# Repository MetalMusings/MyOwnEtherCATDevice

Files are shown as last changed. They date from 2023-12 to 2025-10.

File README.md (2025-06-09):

# MetalMusings EtherCAT device

This repository contains the EtherCAT devices I have designed, built and put in use in linuxcnc.

Everything should be here: 
- Schematics, PCB layouts, and what is needed to build the boards.
- Software tools to create an ESI-file and program the ESC eeprom. 
- Software tools to create the application running on a STM32F407VG.
- A big learning curve is hidden in here as well

I have (so far) used two different ESC ICs: LAN9252 and Ax58100. 
Both work, I can't really see a difference. 
The Ax58100 has a leg spacing of 0.4 mm, 0.5 mm for the LAN9252, if that matters.
On paper the Ax58100 has more builtin functionality like stepper motor drivers,
but the documentation is lacking. Or my understanding of the documentation is lacking.
The Ax58100 supposedly has more efficient access to registers and data.
The indirection scheme is the main objection to using LAN9252, I have read.
The LAN9252 is the true and tested IC of the two. If you don't know, go for the LAN9252.

The EtherCAT cards, which I call EaserCAT cards, use an EtherCAT chip and a normal MCU.
I have used the STM32F407VGT6. The EaserCAT chip does the network talk and other 
EtherCAT things. The STM32 does the application things, like reading and setting pins high or low,
reading encoder inputs, generate stepper motor pulses and other interesting applications one can think of.
There is a narrow interface between the two: SPI and a couple of lines for synchronization.
Any decent MCU can do that, it doesn't have to be a STM32F407VGT6. I have tested with a esp32 with success.
Feel free to experiment with other processors.

I learned most of what I know about EtherCAT through a number of Youtube videos I made.
There are accompanying git branches. For example, for video 8 you can check out the
Video8 branch to get the software tree in the state at the video.
More info on the videos, which are now more of historical interest, but also a bit of learning by following [this link](Videos.md)

And of course, this work builds on the work of many others. This would not be possible without their work. 
I'm just reusing what they did and maybe expanding on it.

Here is the start of [building instructions](Build.md)

## EaserCAT 2000 - a testbench for ESC+MCU, SOES, stepper generator, linuxcnc

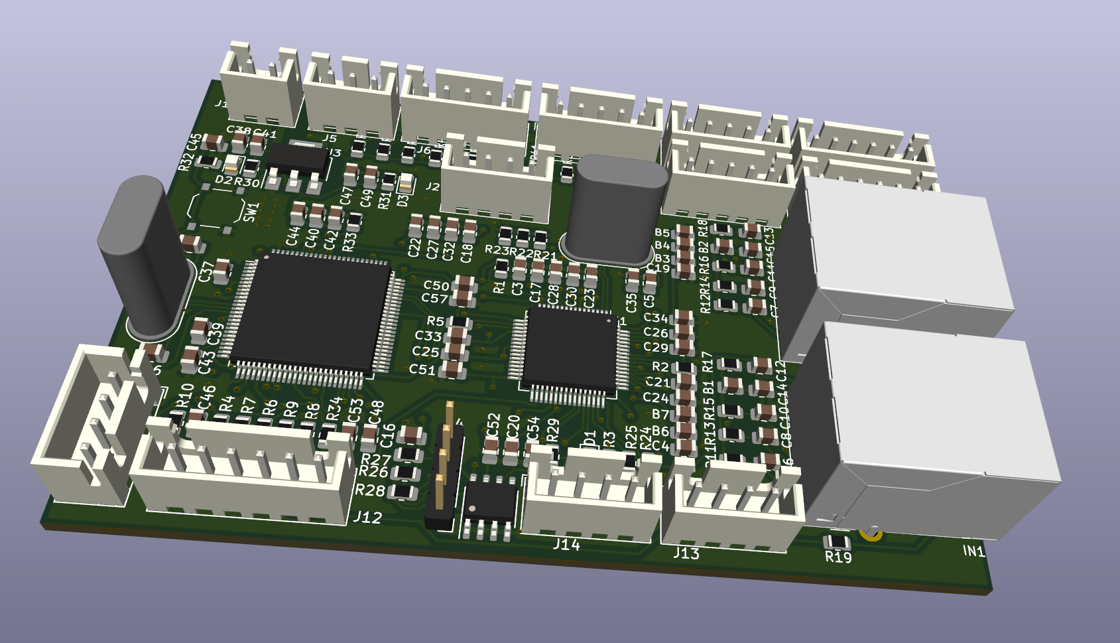
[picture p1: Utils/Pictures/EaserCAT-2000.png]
Picture of EaserCAT 2000 board


This was the first card that got used in Linuxcnc. Follow [link here](Cards/EaserCAT-2000/)
I think I got it working pretty well in the end. There was, and still is, an issue with
synchronization between the linuxcnc servo-loop and the ESC DC loop.
I don't remember the status of it anymore, it was some time ago I worked with it.
The main thing was that it lacked optocouplers and isolation for the external signals.

## EaserCAT 3000 - All in one board with Ax58100

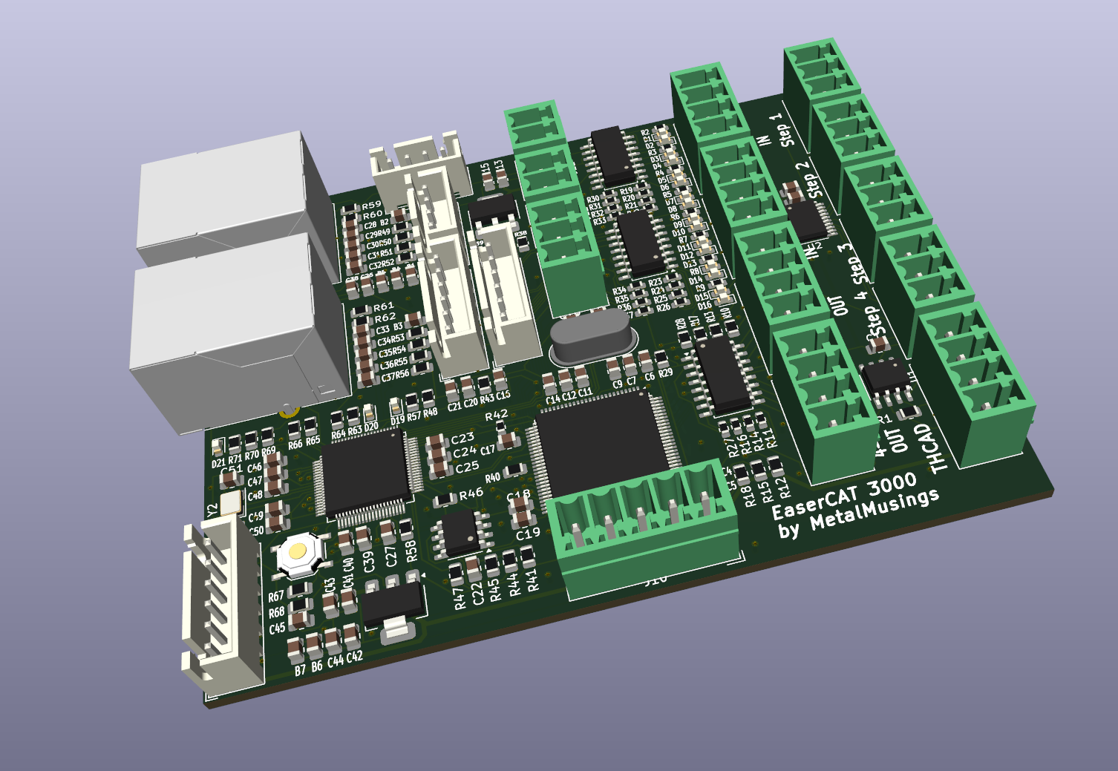
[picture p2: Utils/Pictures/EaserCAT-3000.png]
Picture of EaserCAT 3000 board


This card is an evolution of the EaserCAT 2000 and was intended to be used in my plasma cutter.
It features four stepper driver outputs, input for a THCAD arc voltage card, an encoder, 
an analog output (for spindle +- 10V), eight digital inputs, four digital outputs, 
plus some 12 I/O for any possible extension. The IOs are isolated from the MCU.

However, I couldn't get this card to work, almost at all. The Ax58100 didn't even load the eeprom. 
Struggling with the documentation for the Ax58100, which formed my negative opinion about that,
I gave up and let it sit for over half a year. It was first when someone came and asked 
questions around it I had another look. I built a new board, and it all started to work.
At time of writing it all seems to work.

The latest vesion of the firmware has all parameters for step generators as PDOs.

[Link here](Cards/EaserCAT-3000-Digital-Stepper-Analog-Encoder-Frequency/)

## EaserCAT 4000 - THCAD reader

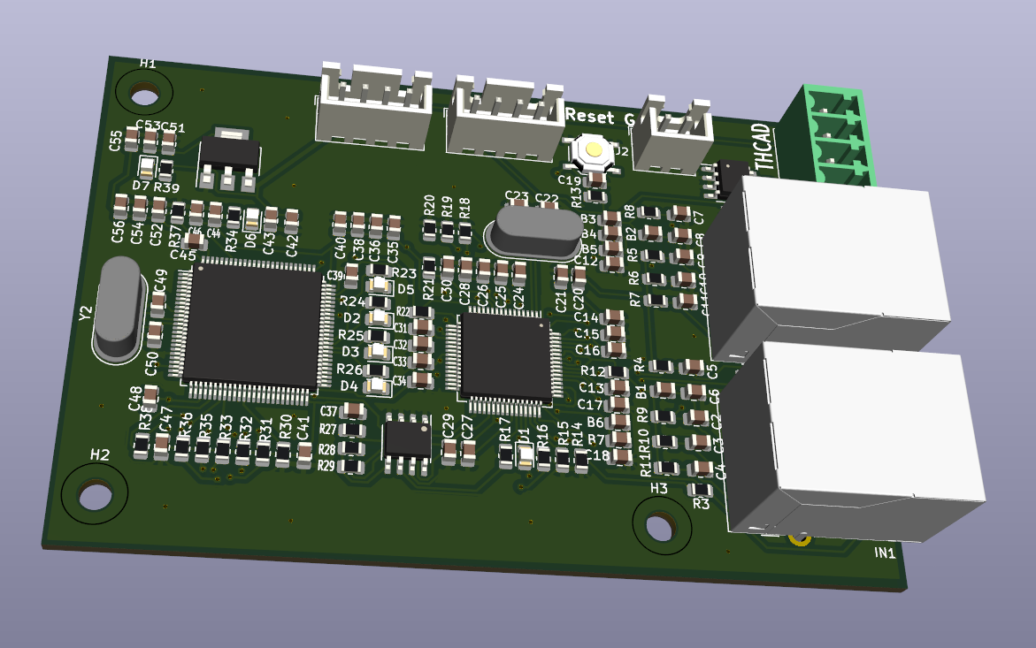
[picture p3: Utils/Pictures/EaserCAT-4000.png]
Picture of EaserCAT 4000 board


Faced with the problems with the EaserCAT 3000 board, and still wanting to use EtherCAT 
in my upcoming plasma cutter, I made this board whos single purpose is to read 
the PWM frequency from Mesa's THCAD board.\
The THCAD board reads the voltage between 
the plasma torch and the workpiece which is around 100V. Highly isolated, and with 
a voltage to frequency converter it delivers a differential pwm signal. 
The frequency of this signal can be related to the voltage.\
That's what is needed for linuxcnc torch height control.

In the tests on the bench this can read at least up to 200 kHz, but its's better to be below 100 kHz.
The THCAD has a frequency divider one can set to make the frequency range nicely match this.
It seems to work fine so far. 
Implementation is with interrupts. \
A better option would have been to use TIM2's PWM_INPUT function, which can work with several MHz frequency. 
I tried the PWM_INPUT method a lot but couldn't get it to work. The current method still works, though.
If time and interests are in phase with the moon, I might look at PWM_INPUT again.

This board is now relegated to history, replaced by the EaserCAT-6000.

[Link here](Cards/EaserCAT-4000-THCAD-Reader/)

## EaserCAT 5000 - Digital IO without MCU

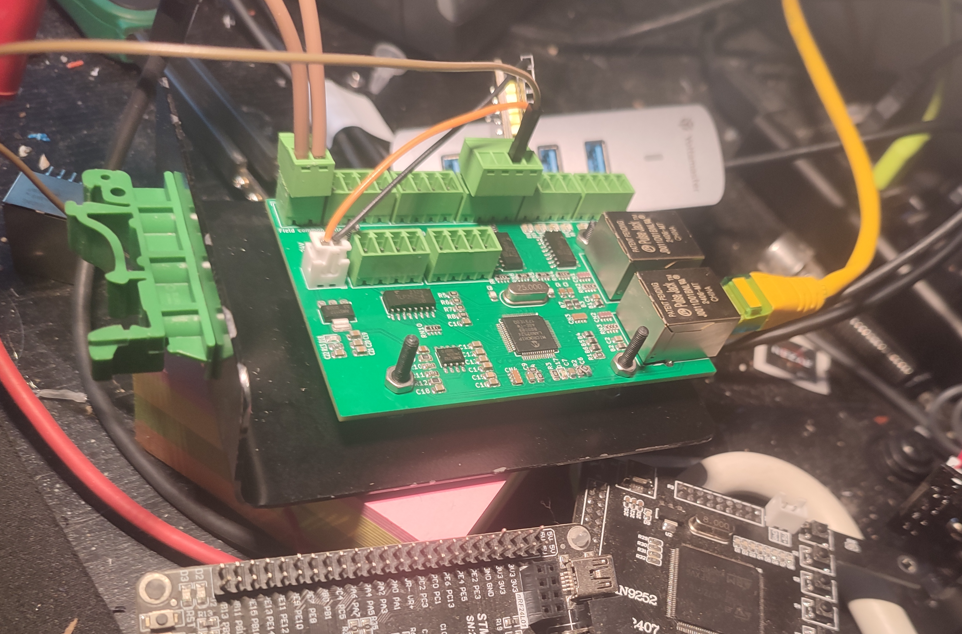
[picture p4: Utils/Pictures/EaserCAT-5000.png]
Picture of EaserCAT 5000 board


A card just doing Digital Input and Digital Output. The intentions were to read 
limit switches and some other switches around the plasma torch. And to switch on the plasma torch.
It's a single LAN9252, configured for local IO. Optocouplers are attached to IO pins for isolation.
It has been tested on the bench, it works with TwinCAT.

HOWEVER, it doesn't work, and will not work, with linuxcnc. As I've learned,
the IgH EtherCAT master needs a CoE client (CANopen over EtherCAT).
The LAN9252 in DIO mode is only an EtherCAT client and can't be turned
into a CoE client. And the IgH EtherCAT application interface for real-time
communication can not be downgraded to work with a pure EtherCAT client,
it requires a CoE client.

To add CoE functionality means to add number of objects at certain positions
in the client and that can not be done to the LAN9252. It is what it is.
In a setup with LAN9252 with MCU, those objects are created in the firmware,
so there it works.

This board is now relegated to history, replaced by the EaserCAT-6000.

## EaserCAT 6000 - Digital IO and frequency input

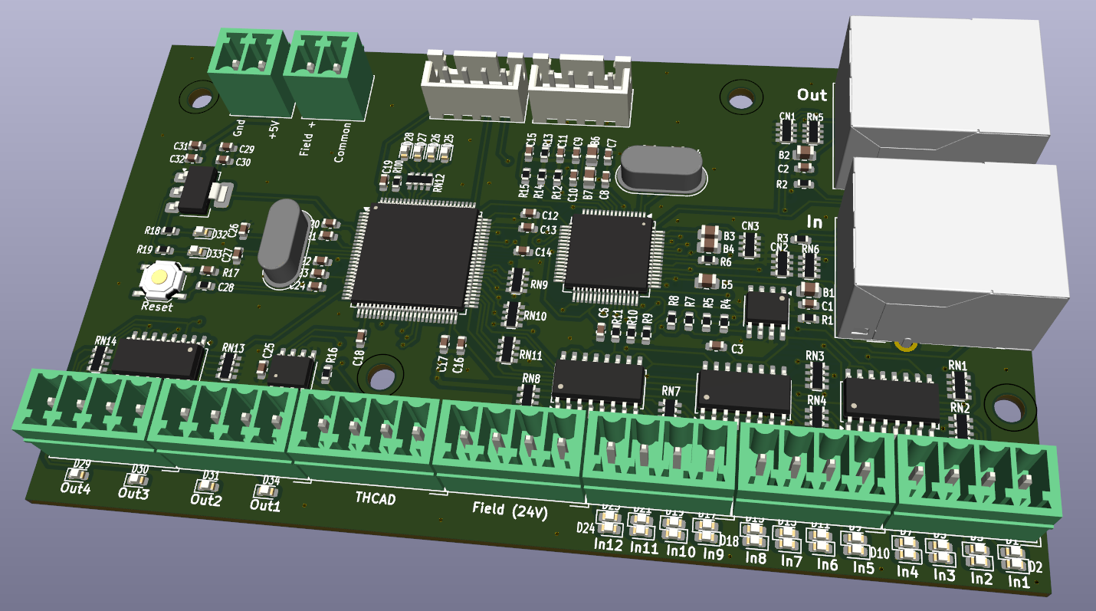
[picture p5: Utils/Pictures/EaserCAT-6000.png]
Picture of EaserCAT 6000 board


Finally, a card that's actually used in a real system. This card is used in my plasma cutter. 
It has 12 digital inputs, 4 digital outputs and a frequency counter to get
the input from Mesa's THCAD (reader of voltage between plasma nozzle and workpiece).\
All digital IOs are opto-isolated and the frequency input uses a RS-485 receiver.

In the plasma cutter, it does the job. There are three ECT60 stepper motor drivers.
And the EaserCAT-6000 card. It handles limit switches for X, Y and Z, floating switch,
break-away switch, and plasma Arc OK signal. There is room for e-stop and other switches.\
The plasma torch is switched on using one of the digital outputs.\
THCAD is an older model with full voltage input. Frequency divider is set to 1/32.

This board replaces EaserCAT-4000 and EaserCAT-5000. 

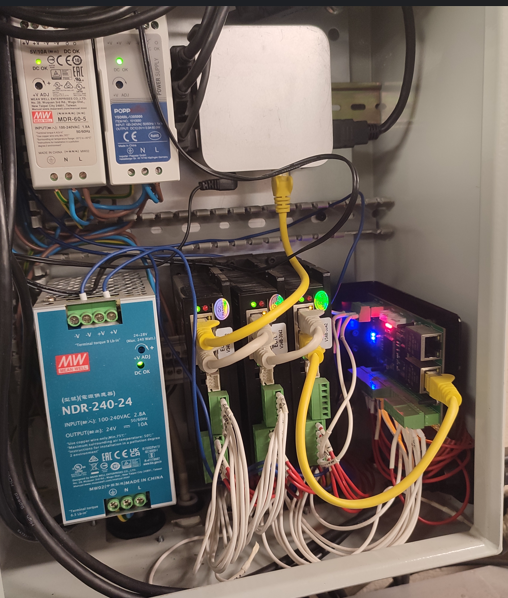
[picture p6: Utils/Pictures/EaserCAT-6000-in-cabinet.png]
Inside the cabinet


[Link here](Cards/EaserCAT-6000-THCAD-reader+Digital-IO/)

A few weeks later and I've used this card in the plasma cutter for quite a bit of cutting and it hasn't missed a beat. Works so well. THC follows the sheet surface up and down. Awesome.

## EaserCAT Torch Height Control - EaserCAT 7000 with THTIC and THTIC2

Actually something useful again - not one, but two, plasma torch voltage readers.
They replace the THCAD board and comes with the entire chain from voltage reading to the introduction of a calibrated voltage to linuxcnc for use in QtPlasmaC. 

Let's start with the plasma cutter. There is either a THTIC or THTIC2 mini-board, which reads the plasma torch voltage, and through a voltage divider lowers it to about 2 Volts during cutting. This voltage is converted by an analog to digital converter and feeds the digitized voltage to the EaserCAT 7000 board via an I2C bus (cable). The EaserCAT 7000 board makes the voltage available both as the raw read voltage for further scaling, or as a calibrated voltage using entered calibration constants.

The plasma torch voltage is DCEN - DC Electrode Negative. The workpiece ground is often connected to ground/earth.
With ground as the reference voltage, the plasma torch voltage ranges between 0 V and -200 V.
An inverting operational amplifier switches the polarity for the ADC. The ground planes on the circuit board are connected to the workpiece ground.

An important feature of THCTIC and THCTIC2 is that the plasma voltage side is isolated from the linuxcnc signal side. The isolation level is better than 1.5 kV. This is achieved by an I2C isolator and an isolated DC-DC converter. The difference between the two cards is the choice of ADC. THTIC uses MCP3221 and THTIC2 uses ADS1014. Both are 12-bit analog to digital converters, ADS1014 is perhaps an 11-bit, both with sampling rates around 3 kHz. A newly measured voltage value can be obtained every 1 ms. Of course you only choose one of the two. Since it seemed pretty easy when I did it, I made two different ones. Always good to have options.

The boards are relatively small, 42x30 mm. Voltage 5V in, current less than 10 mA. I2C Data and clock. 

### THTIC
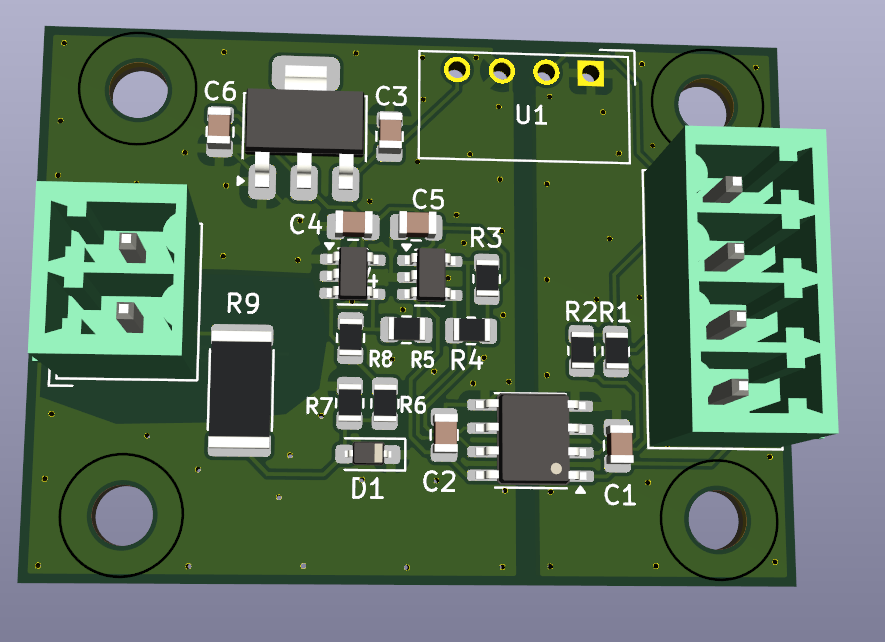
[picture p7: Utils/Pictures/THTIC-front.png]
THTIC
 
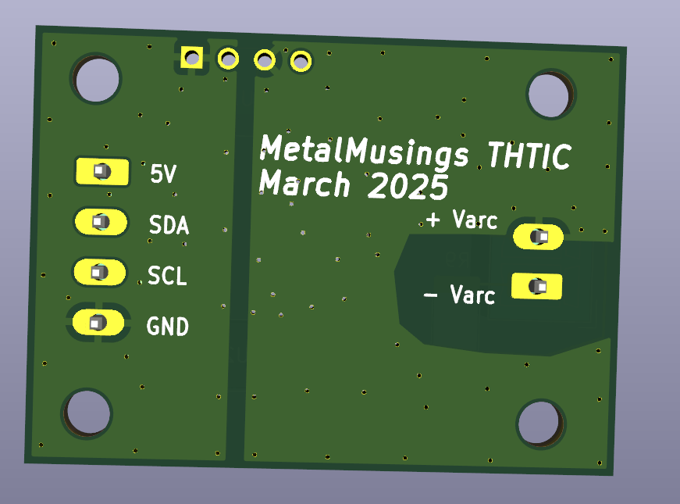
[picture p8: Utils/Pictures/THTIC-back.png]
THTIC


### THTIC2
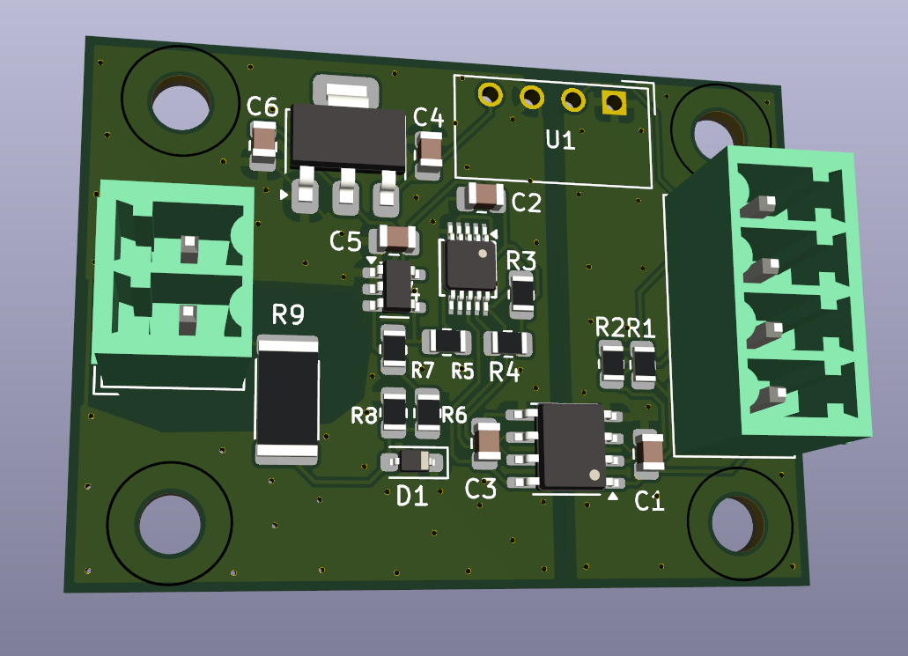
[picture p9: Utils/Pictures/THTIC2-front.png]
THTIC2
 
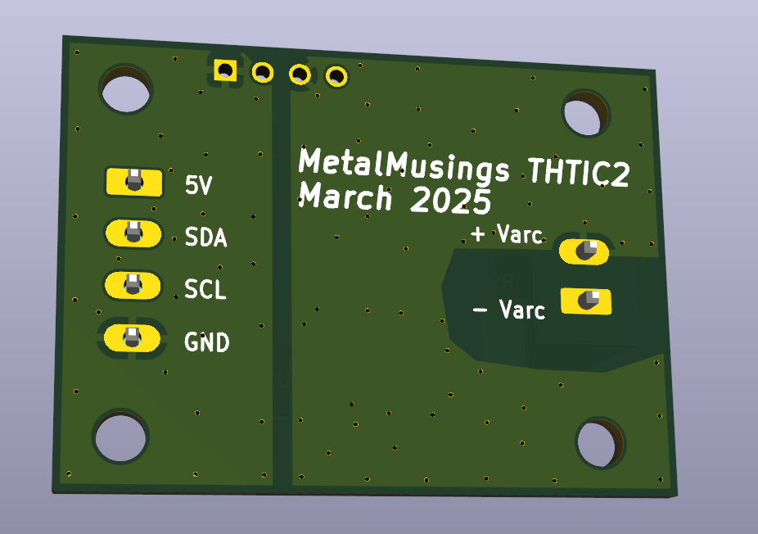
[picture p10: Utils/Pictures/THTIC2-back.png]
THTIC2


### EaserCAT-7000 Digital IO and I2C voltage reader
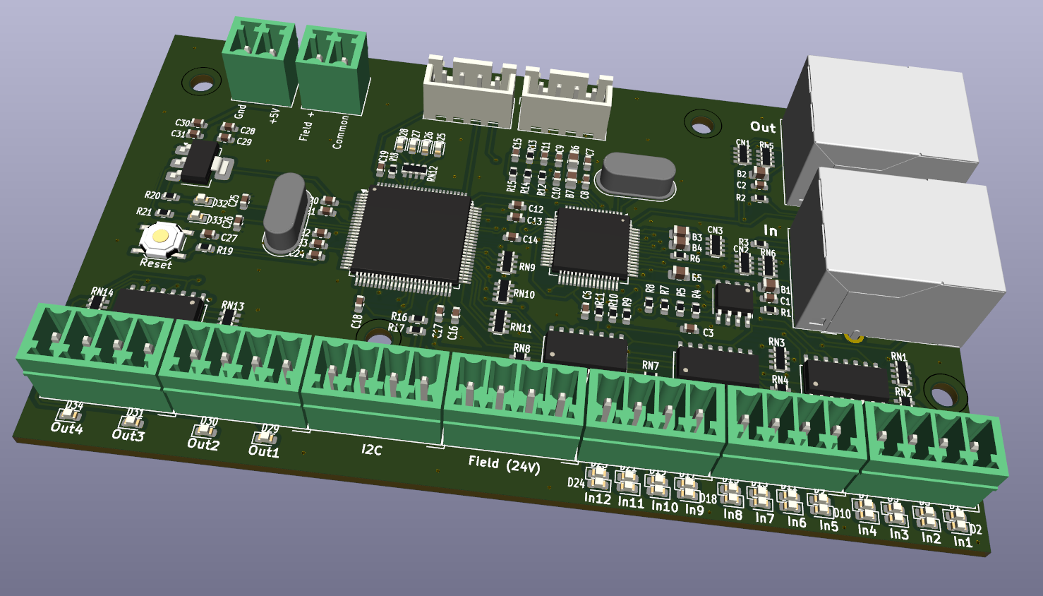
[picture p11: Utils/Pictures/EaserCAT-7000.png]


EaserCAT-7000 is an EaserCAT-6000 board where the THCAD frequency input has been replaced by the I2C bus.
There are twelve digital inputs and four digital outputs.

Currently the EaserCAT-7000 can handle two I2C voltage readers, on different I2C addresses.\
Configuration of the connected I2C devices is done by setting the voltage reader type in SDOs 0x2000:1 and 0x2001:1 for device 1 and 2. The I2C device type is set to 0 by default. A zero means no I2C ADC. Entering a 1 in 0x2000:0 selects the MCP3221, and a 2 in 0x2000:0 selects the ADS1014.\
The I2C address for the ADC is written into SDOs 0x2000:2 and 0x2001:2. The address for the MCP3221 is selected when it is purchased - there are 8 different models each with a different I2C address 0x48-0x4f. The THTIC2 board has the address fixed at 0x48; can be modified during pcb assembly to 0x49 quite easily - check datasheet. Short version is to cut Addr-Gnd and add Addr-Vcc.

Pay attention to the polarity when connecting the plasma voltage leads the THTIC and THTIC2. Varc+ must have higher voltage potential the Varc- (as one would expect). The voltage divisor may need to be adjusted, there is now one 100 kOhm resistor and a 2.2 kOhm resistor, which brings down 100 V to around 2 V. Adjust as needed. For high voltage, pay attention to the max allowed voltage of the resistor. The ADC likes to have around 2-3 Volts when cutting.

The experience with these cards has been very good. I used the THTIC a lot, cutting for at least an hour of cutting time, with THC enabled and active. A status variable shows that it has been working the whole time, no stops or resets. After that I switched to the THTIC2 card and have been using that since. Works really well.

## THCLIP Enable ohmic sensing with the IPTM-60 torch

This is for the torches known as IPT-60 PT-60 S45 IPTM-60 IPTM-80 and many more that have blowback start with the torch tip exposed and normally shortened to the torch electrode. Normally this torch can't use ohmic sensing since all parts are connected to ground. At least on my machine, a Herocut 8000, the blowback start cable from the torch can be cut during sensing. This enables ohmic sensing and it continues to operate in other situations.

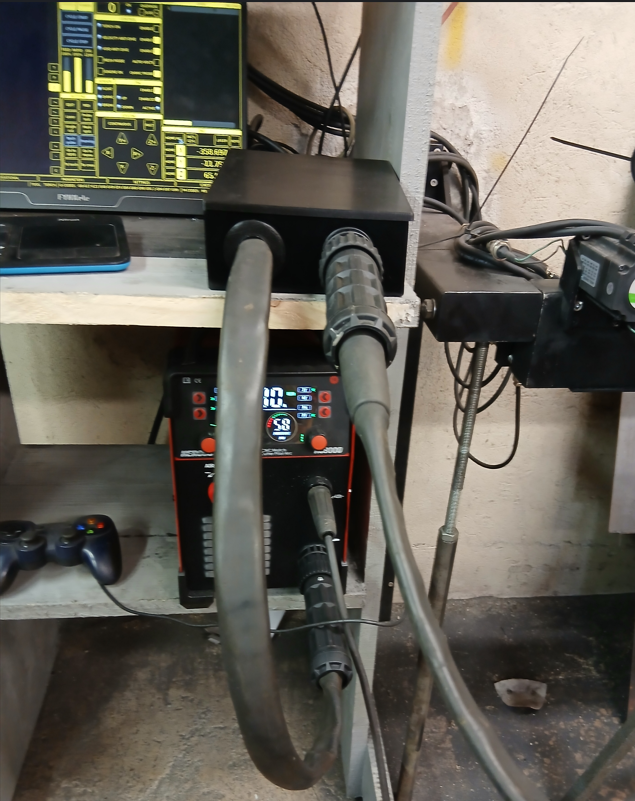
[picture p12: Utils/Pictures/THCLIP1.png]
THCLIP


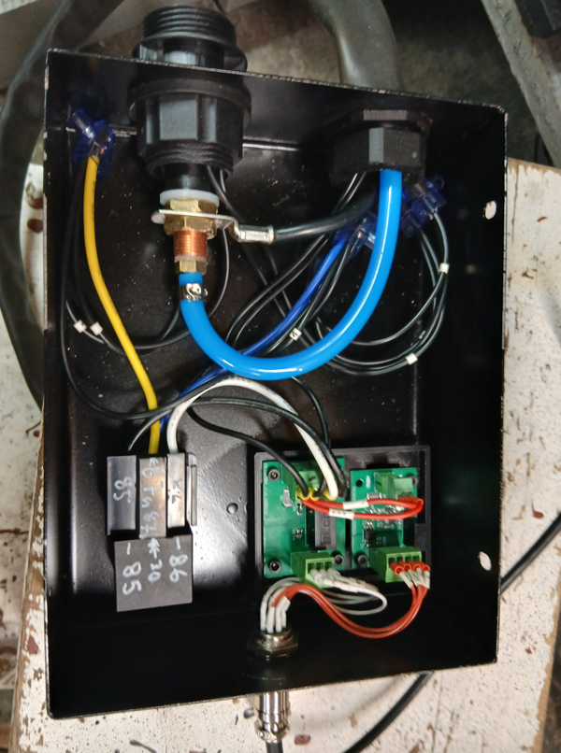
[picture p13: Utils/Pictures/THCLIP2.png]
THCLIP


I tried at first to use the normal Arc voltage reader to detect any contact between the torch and the work piece during probing. However, that was not reliable - it seems there is electronics involved with the arc voltage. Don't want to know details. 

I put a second voltage reader THTIC2 close to the THCLIP and measure the 24V applied after the relay. Monitoring this voltage turns out to be reliable and makes the ohmic sensing work really well.

I have made an adaptation to the EaserCAT 7000 to handle the contact. The relay has a short, some 10 msecs, setup time. The read voltage must therefor first go above the voltage limit before it starts to scan for the voltage to go below the voltage limit which indicates contact.

The Trafimet torch hose connectors are called FY0022 and FY0023. The relay is a 24V 40A standard car relay. Check out the Kicad schematics for the other parts.

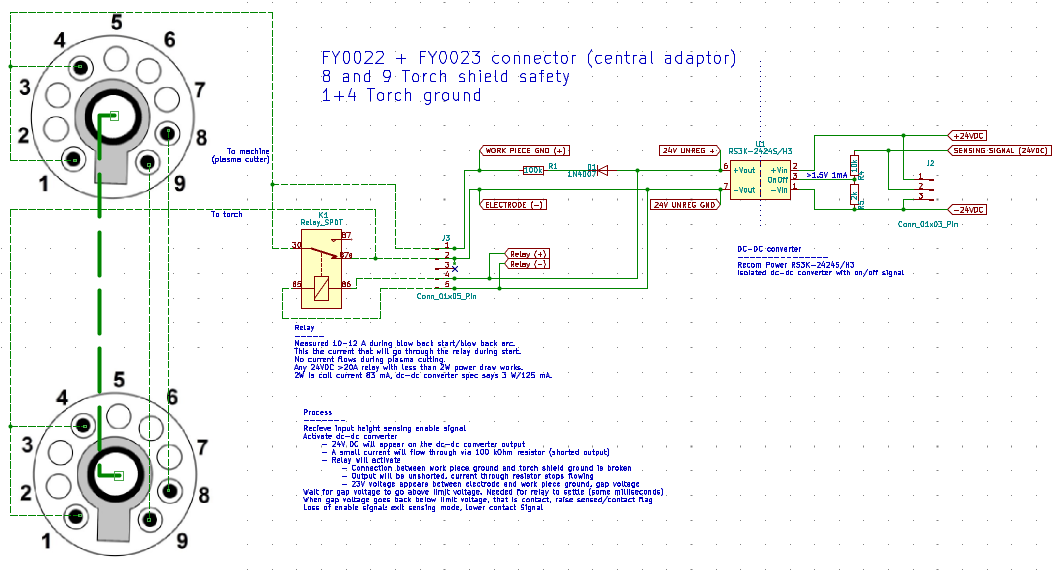
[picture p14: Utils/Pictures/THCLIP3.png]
Schema

Leads 1 and 4 are the blowback arc start ground leads in my torch. They get cut by the relay during ohmic sensing. Voltage is measured on connector J3, between pin 1 and pin 2.

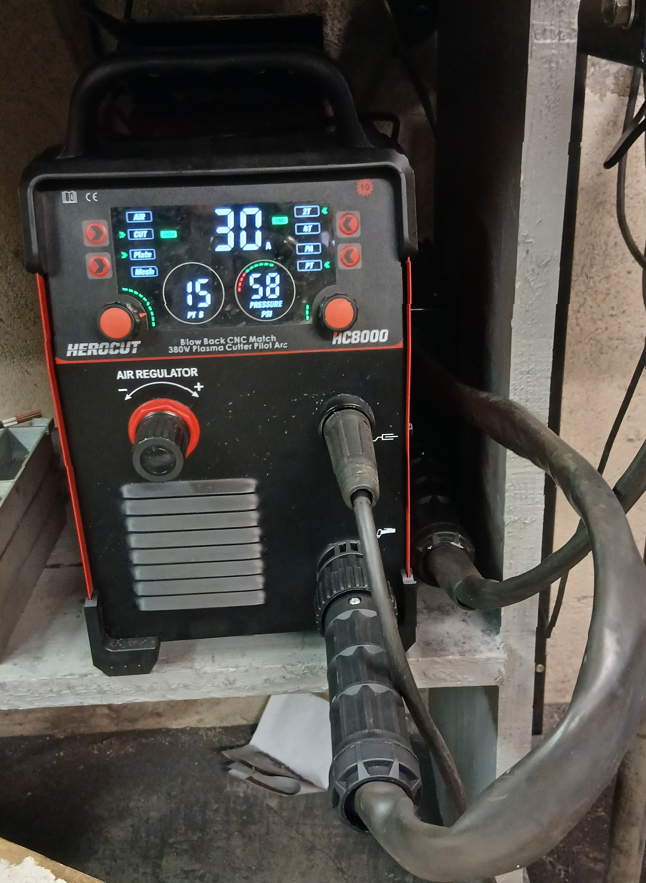
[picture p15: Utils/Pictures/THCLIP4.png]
Ready for use


## License

Don't violate the original licenses. No warranties. Use it any way you like.\
Remember: It is a hobby project, not a product.

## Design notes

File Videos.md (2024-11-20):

# Making my own EtherCAT device

This repository contains software, pcb shematics and layouts, reference documentation etc
that I used during the creation of my own EtherCAT device.

This job is documented in a series of Youtube videos, from my first attempts to understand
how EtherCAT works, to making my own pcb, program it and testing it in LinuxCNC.

=======
The links are now pointing to nowhere. Checkout a Video branch,  Video8, and it might work
=======

## Make my own EtherCAT device 9. About time. Step generator

This was something, I almost gave up. But here it is. A working step generator.
Actually, not one but two step generators for the EaserCAT 2000 board.
For a step generator it is all about timing, timing and timing.
I'll walk you through what I had to do to get it to work.
It can give some general insight into how EtherCAT for linuxcnc works.

Biggest changes this time are in the [Firmware folder](Firmware).
The [Documentation folder](Documentation) has design details on the second step generator.
A small but fatal indexing bug was fixed in the EEPROM_generator.
For all details, read the git log. Too much to mention all.

Watch the video (https://youtu.be/lBDBcseFki8)

## Make my own EtherCAT device 8. EaserCAT 3000

Introducing the new **EaserCAT 3000** board. It's an evolution of the EaserCAT 2000
and intended to be used in my plasma cutter. It features four stepper driver outputs,
input for a THCAD arc voltage card, an encoder, an analog output (for spindle +- 10V),
eigth digital inputs, four digital outputs, plus some 12 I/O for any possible extension.

The KiCAD files are in the [KiCAD folder](Kicad/Ax58100-stm32-ethercat)

Watch the video (https://youtu.be/boanv6ihYtI)

## Make my own EtherCAT device 7. Turning in the lathe

I have now put things together so the EaserCAT 2000 card controls
my small CNC lathe. Two stepper generators, one each for the X and Z axes,
and an encoder counter for the spindle encoder are on this small card.

While it works there are still issues caused by the variation in cycle time. Thankfully
I was able to reduce the variation from 80-100 microseconds down to 2-3 microseconds,

Watch the video (https://youtu.be/Bqi1KXEVI1Q)

## Make my own EtherCAT device 6. Stepper motor driver

The stepper driver generator shows up and makes some stepper motor sounds. The two big things
this time have been setup of the timer for the stepper pulses and synchronizing the EtherCAT
cycle with the linuxcnc servo-thread cycle. Thankfully I don't show much of that.

Watch the video (https://youtu.be/QNNEA0wO4Mw)

## Make my own EtherCAT device 5. The lathe is alive

I hook up the EaserCAT 2000 board to my mini-lathe and make it work.
Documentation is available here, please select the *Video5* branch.

Watch the video (https://youtu.be/wOtMrlHCCic)

## Make my own EtherCAT device 4. The PCB is here

In this video it starts to be interesting. I have got the pcb and I try to make it work.
Now I finally make documentation available, see [this folder](Pcb-1-lan9252).

Watch the video (https://youtu.be/An0VrKYAv88)

## Make my own EtherCAT device 3. Encoder

I made a rudimentary EtherCAT encoder module. To test it I need something better than my test setup so I start to design my own PCB to be used for testing with LinuxCNC.

Watch the video (https://youtu.be/oNIBOpeTpQ4)

## Make my own EtherCAT device. 2. MCU and SPI

Testing the SPI connection between the MCU and the LAN9252 chip. Get into state diagrams for EtherCAT and for CIA402.

Watch the video (https://youtu.be/F9HdCEG6kow)

## Make my own EtherCAT device. 1 Digital IO

My first tries with the LAN9252 chip. Getting accustomed to some tools.

Watch the video (https://youtu.be/IGmXsXSSA4s)

# EtherCAT PCB based on LAN9252 and STM34F407

##### The firmware is in the **Firmware** folder.

Open this in PlatformIO. PlatformIO might be able to install all necessary software. If not, you need at least Arduino for STM32 (STM32duino) and SPI. PlatformIO might be able to figure that out, I hope so.
SPI settings are in lib/soes/hal/spi.cpp if you are interested.
SOES is the Arduino port of SOES from <https://github.com/kubabuda/ecat_servo/tree/main/examples/SOES_arduino>
My own code is in main.cpp. The encoder counter code is in STM34_Encoder.cpp

###### The PCB design is in **Kicad**.

Open this with Kicad. I have put the symbols and footprints in there, just set the right paths.
The design is in the state I ordered the pcb from Aisler, Germany.

###### The **Schematics** folder

contains reference documentation, schematics of several LAN9252 evaluation boards and other boards. This is from where I got inspiration and ideas to the design. No I didn't read all the reference documentation - I copied most from these designs and that's why it also worked the first time. [Freerouting](https://github.com/freerouting/freerouting) was used to route the pcb. Normally I route the nets by hand but this time it was a bit much and it came out quite nice and, most importantly, it worked. 

##### ESI xml file generator is in **EEPROM_generator**.

Access the folder with a file browser and click on index.html to make or update your own xml file (and other necessary files, incl eeprom bin). Copy the contents to Firmware/lib/soes
and to Twincat esi xml file directory `c:\twincat\3.1\io\modules\ethercat`
The original EEPROM_generator is found here <https://github.com/kubabuda/EEPROM_generator>

##### **CubeMX-files** are for reference only.

The .ioc file can be opened in CubeMX. The STM32F407 processor has functions tied to specific pins, the .ioc file has this info. This is just for reference.

##### ESI (EtherCAT Slave Information) files

I have put [Dig_8IN_8OUT.xml](Dig_8IN_8OUT.xml) here, this is an example ESI file for the LAN9252 IC standalone, no MCU needed. It's sometimes handy to have the simplest possible ESI file at ahnd, here it is. You find the ESI file for the Encoder application [here](Firmware/lib/soes/MetalMusings_EaserCAT_2000_encoder.xml)

##### **linuxcnc** contains modifications to make EaserCAT 2000 work

The configuration files and the hal component I used are placed here.

##### LAN9252_eeprom_store_valid

Arduino sketch to program the AT24C32 eeprom with a valid eeprom content. Hook up the eeprom using I2C and run the program. The verification in the of theprogram must be passed for valid programming.

###License

Don't violate the original licenses. No warranties. Use it any way you like.

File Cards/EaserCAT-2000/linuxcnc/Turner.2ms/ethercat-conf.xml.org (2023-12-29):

<masters>
  <master idx="0" appTimePeriod="1000000" refClockSyncCycles="5">
    <slave idx="0" type="EK1100"/>
    <slave idx="1" type="EL1008"/>
    <slave idx="2" type="EL2008"/>
    <slave idx="3" type="EL5101"/>
    <slave idx="4" type="generic" vid="00000a88" pid="0a880002" configPdos="true">
      <dcConf assignActivate="300" sync0Cycle="*1" sync0Shift="0"/>
      <sdoConfig idx="2000" subIdx="0"><sdoDataRaw data ="b8 0b"/></sdoConfig>  <!-- Max motor current (3.0A) -->
      <sdoConfig idx="2003" subIdx="0"><sdoDataRaw data ="64 00"/></sdoConfig>  <!-- Standby current percentage (100%) -->
      <sdoConfig idx="2011" subIdx="0"><sdoDataRaw data ="00 00"/></sdoConfig>  <!-- Open loop -->
      <syncManager idx="2" dir="out">
        <pdo idx="1600">
          <pdoEntry idx="6040" subIdx="00" bitLen="16" halPin="cia-controlword" halType="u32"/>
          <pdoEntry idx="6060" subIdx="00" bitLen="8" halPin="opmode" halType="s32"/>
          <pdoEntry idx="607A" subIdx="00" bitLen="32" halPin="target-position" halType="s32"/>
          <pdoEntry idx="60FF" subIdx="00" bitLen="32" halPin="target-velocity" halType="s32"/>
        </pdo>
      </syncManager>
      <syncManager idx="3" dir="in">
        <pdo idx="1a00">
          <pdoEntry idx="6041" subIdx="00" bitLen="16" halPin="cia-statusword" halType="u32"/>
          <pdoEntry idx="6061" subIdx="00" bitLen="8" halPin="opmode-display" halType="s32"/>
          <pdoEntry idx="6064" subIdx="00" bitLen="32" halPin="actual-position" halType="s32"/>
          <pdoEntry idx="606C" subIdx="00" bitLen="32" halPin="actual-velocity" halType="s32"/>
          <pdoEntry idx="6077" subIdx="00" bitLen="32" halPin="actual-torque" halType="s32"/>
        </pdo>
	</syncManager>
    </slave>
    <slave idx="5" type="generic" vid="00000a88" pid="0a880002" configPdos="true">
      <dcConf assignActivate="300" sync0Cycle="*1" sync0Shift="0"/>
      <sdoConfig idx="2000" subIdx="0"><sdoDataRaw data ="68 10"/></sdoConfig>  <!-- Max motor current (4.2A) -->
      <sdoConfig idx="2003" subIdx="0"><sdoDataRaw data ="64 00"/></sdoConfig>  <!-- Standby current percentage (100%) -->
      <sdoConfig idx="2011" subIdx="0"><sdoDataRaw data ="00 00"/></sdoConfig>  <!-- Open loop -->
      <syncManager idx="2" dir="out">
        <pdo idx="1600">
          <pdoEntry idx="6040" subIdx="00" bitLen="16" halPin="cia-controlword" halType="u32"/>
          <pdoEntry idx="6060" subIdx="00" bitLen="8" halPin="opmode" halType="s32"/>
          <pdoEntry idx="607A" subIdx="00" bitLen="32" halPin="target-position" halType="s32"/>
          <pdoEntry idx="60FF" subIdx="00" bitLen="32" halPin="target-velocity" halType="s32"/>
        </pdo>
      </syncManager>
      <syncManager idx="3" dir="in">
        <pdo idx="1a00">
          <pdoEntry idx="6041" subIdx="00" bitLen="16" halPin="cia-statusword" halType="u32"/>
          <pdoEntry idx="6061" subIdx="00" bitLen="8" halPin="opmode-display" halType="s32"/>
          <pdoEntry idx="6064" subIdx="00" bitLen="32" halPin="actual-position" halType="s32"/>
          <pdoEntry idx="606C" subIdx="00" bitLen="32" halPin="actual-velocity" halType="s32"/>
          <pdoEntry idx="6077" subIdx="00" bitLen="32" halPin="actual-torque" halType="s32"/>
        </pdo>
	</syncManager>
    </slave>
    <slave idx="6" type="generic" vid="00aaa" pid="000bbbccc" configPdos="true">
      <dcConf assignActivate="300" sync0Cycle="*1" sync0Shift="0"/>
      <syncManager idx="2" dir="out">
        <pdo idx="1600">
          <pdoEntry idx="7000" subIdx="00" bitLen="32" halPin="enc-pos-scale" halType="s32"/>
        </pdo>
        <pdo idx="1601">
          <pdoEntry idx="7001" subIdx="00" bitLen="32" halPin="enc-index-latch-enable" halType="u32"/>
        </pdo>
      </syncManager>
      <syncManager idx="3" dir="in">
        <pdo idx="1a00">
          <pdoEntry idx="6000" subIdx="00" bitLen="32" halPin="enc-position" halType="float-ieee"/>
        </pdo>
        <pdo idx="1a01">
          <pdoEntry idx="6001" subIdx="00" bitLen="32" halPin="enc-frequency" halType="float-ieee"/>
        </pdo>
        <pdo idx="1a02">
          <pdoEntry idx="6002" subIdx="00" bitLen="32" halPin="DiffT" halType="u32"/>
        </pdo>
        <pdo idx="1a03">
          <pdoEntry idx="6003" subIdx="00" bitLen="32" halPin="index-byte" halType="u32"/>
        </pdo>
        <pdo idx="1a04">
          <pdoEntry idx="6004" subIdx="00" bitLen="32" halPin="index-status" halType="u32"/>
        </pdo>
      </syncManager>
    </slave>
  </master>
</masters>

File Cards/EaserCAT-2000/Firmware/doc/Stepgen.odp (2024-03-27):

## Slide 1

Position(Real)

stepPosition(Integer)

cycleTime

Time

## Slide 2

Position(Real)

stepPosition(Integer)

Initial condition

”scale” is known = steps/mm

initialPosition

initialStepPosition

cycleTime

Time

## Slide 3

Position(Real)

stepPosition(Integer)

End condition

”scale” is known = steps/mm

initialPosition

initialStepPosition

commandedPosition - 3 examples here

cycleTime

Time

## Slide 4

Position(Real)

stepPosition(Integer)

StepPosition for end

”scale” is known = steps/mm

commandedPosition - 3 examples here

stepPosition =

floor(commandedPosition*scale)

initialPosition

initialStepPosition

cycleTime

Time

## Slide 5

Position(Real)

stepPosition(Integer)

Check for no step

”scale” is known = steps/mm

if initialStepPosition == stepPosition

take no step

goto update and return success

commandedPosition

stepPosition

initialPosition

initialStepPosition

cycleTime

Time

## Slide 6

Position(Real)

stepPosition(Integer)

Check for too many steps

too high frequency

”scale” is known = steps/mm

commandedPosition

stepPosition

initialPosition

initialStepPosition

commandedPosition

stepPosition

approximateFrequency = abs(initialStepPosition - commandedStepPosition)/cycleTime

if approximateFrequency > maxAllowedFrequency

take no step

goto update and return error

cycleTime

Time

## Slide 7

Position(Real)

stepPosition(Integer)

Line equations

”scale” is known = steps/mm

intitialStepPosition != stepPosition

frequency slow enough

commandedPosition

commandedStepPosition

stepPos = k Time + m

k = (commandedPosition - initialPosition)/cycleTime

m = initialPosition

Time = 0 at initial Time (nominal lcnc time)

initialPosition

initialStepPosition

cycleTime

Time

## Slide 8

Position(Real)

stepPosition(Integer)

Check for too flat slope

”scale” is known = steps/mm

intitialStepPosition != stepPosition, must take step

frequency slow enough

commandedPosition

stepPosition

Avoid problems with numerical precision at flat slope.

k * cycleTime * scale = amount of a step to take

if that amount < 0.01 (for example), just take a step in the

right direction half-way into cycleTime.

We know we must take a step due to previous checks.

initialPosition

initialStepPosition

cycleTime

Time

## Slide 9

Position(Real)

stepPosition(Integer)

Tstart

”scale” is known = steps/mm

intitialStepPosition != stepPosition, must take step

frequency range ok

Tstart

For positive k:

Tstart = ((InitialStepPosition+1)/scale - m)/k

For negative k:

Tstart = (InitialStepPosition/scale - m)/k

initialPosition

initialStepPosition

Tstart

cycleTime

Time

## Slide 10

Position(Real)

stepPosition(Integer)

Frequency

”scale” is known = steps/mm

intitialStepPosition != stepPosition, must take step

frequency range ok

Tstart is known

Tstart

initialPosition

initialStepPosition

Frequency = slope of curve, k * scale

Frequency = k * scale

Tstart

cycleTime

Time

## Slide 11

Position(Real)

stepPosition(Integer)

Number of steps

and direction

”scale” is known = steps/mm

intitialStepPosition != stepPosition, must take step

Frequency range ok

Tstart is known

Frequency is known

commandedPosition

commandedStepPosition

nSteps = commandedStepPosition - initialStepPosition

sign(nSteps) = direction

sign(k) = direction

commandedPosition

stepPosition

Tstart

initialPosition

initialStepPosition

Tstart

cycleTime

Time

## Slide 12

Position(Real)

stepPosition(Integer)

Prepare for next cycle

initialPosition <= commandedPosition

initialStepPosition <= commandedStepPosition

initialPosition

initialStepPosition

initialPosition

initialStepPosition

initialPosition

initialStepPosition

cycleTime

Time

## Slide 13

Position(Real)

stepPosition(Integer)

Pulses

Tstart

T=1/frequency

Tstart

Tstart

Tstart

Tstart

cycleTime

Time

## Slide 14

Position(Real)

stepPosition(Integer)

Pulses

Note. Time scale is different in this and following slides

T=0 is measured from SM2 interrupt, which seems to happen within 2-3 μsecs

Therefor, Tjitter = 5 μsecs

Pulse train is defined by

Tstart + Tjitter

frequency

nSteps

cycleTime

Tjitter

Tstart

Tstart

T=1/frequency

Tstart

Tjitter

Tjitter

Tstart

Tstart

Tstart

Time

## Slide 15

Position(Real)

stepPosition(Integer)

Starting the pulse train

Note. Time scale is different in this and following slides

Use HardwareTimer (stm32duino)

Take one of the 1-channel timers 10,11,13,14 on STM32F4 (AN4013)

startTimer->attachInterrupt(startTimerCB); // At constructor time

startTimer->setOverflow(Tjitter+Tstart, MICROSEC_FORMAT); // Now

startTimer->ressume(); //

Let the timer run for Tjitter+Tstart usecs, then it calls startTimerCB (below)

pulseTimer->setMode(pulseTimerChan, TIMER_OUTPUT_COMPARE_PWM2, stepPin);

pulseTimer->setOverflow(uint32_t(frequency), HERTZ_FORMAT);

pulseTimer->setCaptureCompare(pulseTimerChan, 50, PERCENT_COMPARE_FORMAT); // 50%

pulseTimerSteps = abs(nSteps);

pulseTimer->resume();

// Use local copy of nSteps, so it doesn’t accidentally gets overwritten.

cycleTime

Tjitter

Tstart

Tstart

T=1/frequency

Tstart

Tjitter

Tjitter

Tstart

Tstart

Tstart

Time

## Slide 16

Position(Real)

stepPosition(Integer)

Ending the pulse train

Note. Time scale is different in this and following slides

PulseTimer runs and calls pulseTimerCB at end of every PWM pulse

Number of steps to do are counted down and when 0, stop the pulseTimer

--timerPulseSteps;

if (timerPulseSteps == 0)

pulseTimer->pause();

cycleTime

Tjitter

Tstart

Tstart

T=1/frequency

Tstart

Tjitter

Tjitter

Tstart

Tstart

Tstart

Time

Problem with this approach

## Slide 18

Position(Real)

stepPosition(Integer)

The end is unpredictable and collides with next step’s pwm train

Tstart can be predicted accurately

The end of the pulse train also, Tend = Tstart + nStep / frequency

A problem occurs when Tstart,2 happens before Tend (Tstart,2 = Tstart for the next cycle)

At Tstart and Tstart,2 the pwm timer is reloaded. If that happens before the pwm pulse train is finished, problems occur.

At constant speed, every 1 ms we see a part of an overall long pulse train, just take a 1 ms piece and make pulses.

That’s what this procedure does. This works generally fine at constant speed, I think.

At increased and decreased speed, during acceleration, Tstart,2 is not what one think at first. It will be shorter or longer

and the situation described above occurs, when the pwm timer gets reloaded before it is finished.

The rising edge of the pwm pulse is in the right place, but everything that comes may not be.

It can not be like that.

Tend

cycleTime

Tjitter

Tstart,2

Tstart

Tstart

T=1/frequency

Tjitter

Tjitter

Tstart

Tstart

Tstart

Time

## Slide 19

Remedies

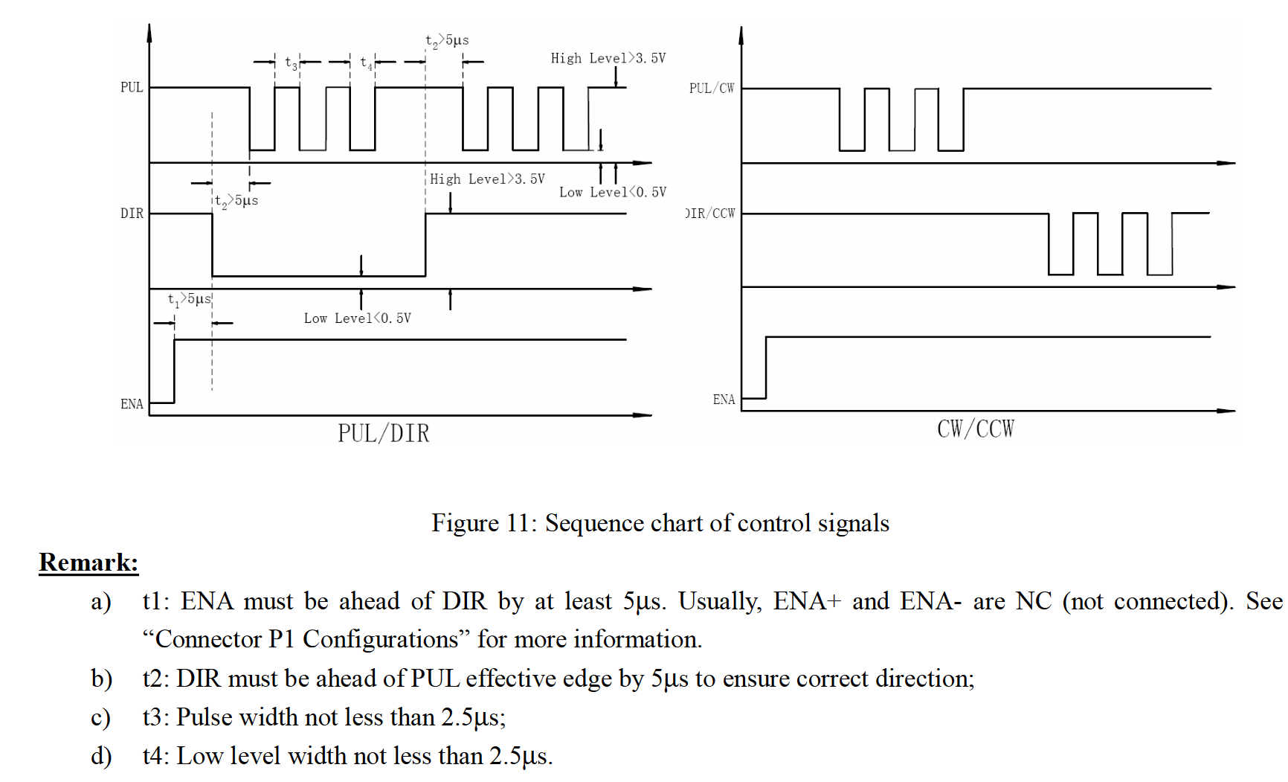
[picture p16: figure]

1. Skip Tstart and distribute pulses inside cycleTime window, keeping clear of the start and end

2. Modify pulse shape to use the most narrow pulse allowed by the driver

3. Don’t check for complete pulse at period update, but on capture/compare.

4. Keep frequency as before

5. Use end time of previous pulse when setting the time for the first pulse

Not perfect.

It will often happen that there are n and n+1 pulses in adjacent cycles. This will result in frequency jumping up and down.

2.5+2.5 usec => 5 usec and max 200 kHz. I don’t need that much. Say 5+5 usecs => max 100 kHz.

cycleTime

Tjitter

T=1/frequency

Interrupt here

## Timer

  >> f=[1 10 20 30 40 50 60 70 80 90 100]*1e3
  f = 1000 10000 20000 30000 40000 50000 60000 70000 80000 90000 100000
- >> fo=[956 9560 18390 27111 35768 44461 53221 61898 70539 79367 88000]
- fo = 956 9560 18390 27111 35768 44461 53221 61898 70539 79367 88000
- >> plot(f,fo, f, f, [f(end) 0],[fo(end) 1000])
- >> k=(fo(end)-1000)/f(end)
- k = 0.8700
- >> m=1000
- m = 1000

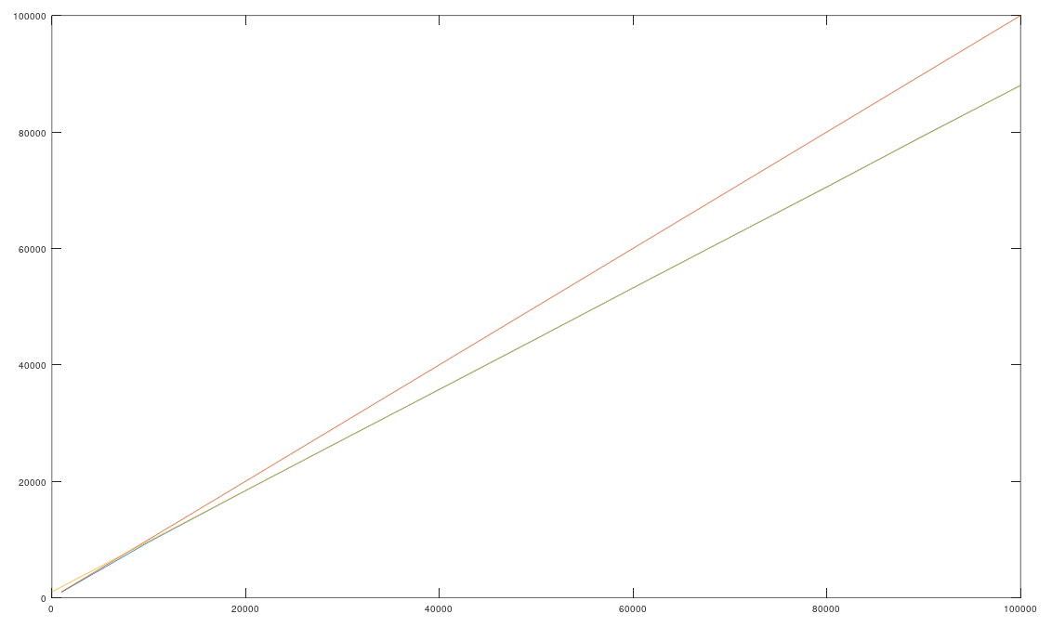
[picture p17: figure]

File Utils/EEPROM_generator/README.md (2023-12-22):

# [🔁 EEPROM generator](https://kubabuda.github.io/EEPROM_generator)

This is basic code generator tool for EtherCAT devices, using [SOES library](https://github.com/OpenEtherCATsociety/SOES).

[It is available online, here](https://kubabuda.github.io/EEPROM_generator)

You can configure:
- ESC (Ethercat Slave Chip) 
- OD (CANopen Object Dictionary) entries
- PDO mappings (which OD objects are mapped in TX, RX datagrams)

Tool generates consistent data across C sources, ESI file and EEPROM content.

It also backs up your current project in localstorage. You can save project to JSON file on your hard drive, restore from it later, and download all files at once.

## Limitations

- Only single, non-dynamic PDO is supported for TX and RX respectively
- Some data types might not be supported
- Browsers other than Firefox might not be supported

If you need more, [RT-Labs](https://rt-labs.com/ethercat/) offers professional IDE - EtherCAT SDK, and training.

# Development

Pull requests welcome.

Source code is intentionally keept in plain Javascript files so that build system like webpack or even web server is not needed.
The only dependency is web browser, that should future proof it.

## [Unit tests](https://kubabuda.github.io/EEPROM_generator/tests.html)

[Unit tests](https://kubabuda.github.io/EEPROM_generator/tests.html) are using [Jasmine](https://jasmine.github.io). 

## OD structure

OD is keept as JSON object. Expected data format:

```js
{
    '1000': { otype: OTYPE.VAR, dtype: DTYPE.UNSIGNED32, name: 'Device Type', value: 0x1389 },
    '1008': { otype: OTYPE.VAR, dtype: DTYPE.VISIBLE_STRING, name: 'Device Name', data: '' },
    '1009': { otype: OTYPE.VAR, dtype: DTYPE.VISIBLE_STRING, name: 'Hardware Version', data: '' },
    '100A': { otype: OTYPE.VAR, dtype: DTYPE.VISIBLE_STRING, name: 'Software Version', data: '' },
    '1018': { otype: OTYPE.RECORD, name: 'Identity Object', items: [
        { name: 'Max SubIndex' },
        { name: 'Vendor ID', dtype: DTYPE.UNSIGNED32, value: 600 },
        { name: 'Product Code', dtype: DTYPE.UNSIGNED32 },
        { name: 'Revision Number', dtype: DTYPE.UNSIGNED32 },
        { name: 'Serial Number', dtype: DTYPE.UNSIGNED32, data: '&Obj.serial' },
    ]},
    '1C00': { otype: OTYPE.ARRAY, dtype: DTYPE.UNSIGNED8, name: 'Sync Manager Communication Type', items: [
        { name: 'Max SubIndex' },
        { name: 'Communications Type SM0', value: 1 },
        { name: 'Communications Type SM1', value: 2 },
        { name: 'Communications Type SM2', value: 3 },
        { name: 'Communications Type SM3', value: 4 },
    ]},
}   
```

OD model for generator has 4 sections:

- `sdo`, not mapped to PDOs
- `txpdo`, mapped to TXPDO (SM3). Expected format (for OTYPE VAR):
```js
{
    '6000': { otype: OTYPE.VAR, dtype: DTYPE.UNSIGNED32, name: 'TXPDO', value: 0x1389, pdo_mappings: ['tx'] },
}
```
- `rxpdo`, same as above, but `pdo_mappings: ['rx']`
- mandatory objects. These are added at code gen stage, with values populated form UI controls.

Code generation copies all values into single OD, adds PDO mappings and SM assignments. 

## PDO mappings

Currently single, non-dynamic PDO is supported for TX and RX respectively.

## Binary file comparison tool for Windows: [VBinDiff](https://www.cjmweb.net/vbindiff/VBinDiff-Win32)

```cmd
VBinDiff et1100.bin  lan9252.bin
```

# TODO

- add support for 64bit number types
- why default dark mode has dark text in Chromium but not Firefox, when OS is in dark mode
- generate .h file for EEPROM emulation
- add support for LAN9253 Direct, XMC4300, XMC4800
- check output for boolean ARRAY
- check output for VISIBLE_STRING ARRAY
- check output for VISIBLE_STRING RECORD subitem
- dynamic/multiple PDOs
- more unit tests
- SM2 offset: regardles of value set, SDK generates RXPDO mappings as SDO1600. SM2 offset change affects
    - `ecat_options.h` #define SM2_sma, MAX_TXPDO_SIZE and MAX_RXPDO_SIZE
    - `esi.xml` `<Sm ControlByte="#x24" Enable="1" StartAddress="#x1600">Outputs</Sm>`
    currently this tool mirrors SDK behavior, check if this hack is needed or just duplicated SDK bug
- calculate `MAX_RXPDO_SIZE`, `MAX_TXPDO_SIZE` based on selected SM2 offset
- modular device profile
- set project name from device name
- DC config in ESI .bin

- use [XML parsing](https://www.w3schools.com/xml/xml_parser.asp) for cleaner builiding ESI XML output
- read XML files: make reverse eningeering 3rd party devices easier
- add indexes list to OD model, to decrease parametes count in methods
- 0x1001 UINT8 Error Register is mandatory according to CiA DS301
- 0x1C12/0x1C13 `PdoAssign` and 0x1608/0x1A08 `PdoMapping` [should be RW](https://infosys.beckhoff.com/english.php?content=../content/1033/el6695/1317558667.html&id=)

### Code optimization

- reuse repeated string constants in objlist.c names, test if does any good or compiler does that for you anyway

# Disclaimer

The EtherCAT Technology, the trade name and logo "EtherCAT" are the intellectual
property of, and protected by Beckhoff Automation GmbH.

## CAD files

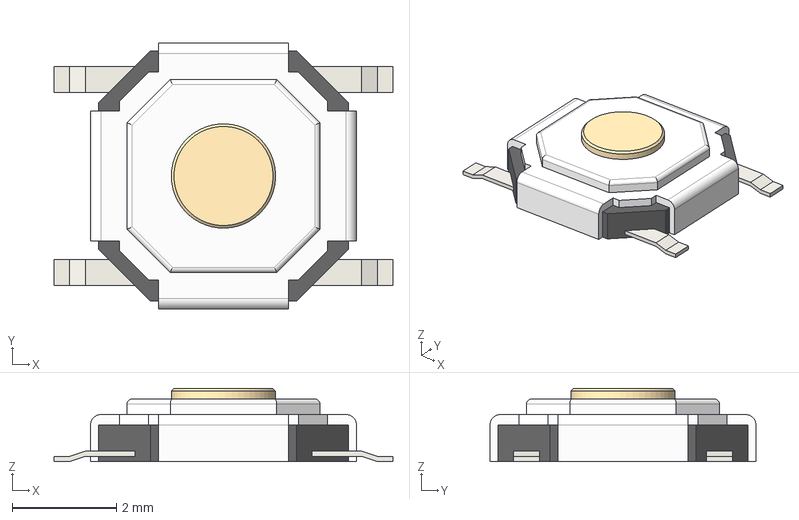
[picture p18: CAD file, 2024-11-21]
Cards/EaserCAT-7000-DIO+I2C/Kicad/Models/TS-1187A.step
6.50 x 5.10 x 1.40 mm

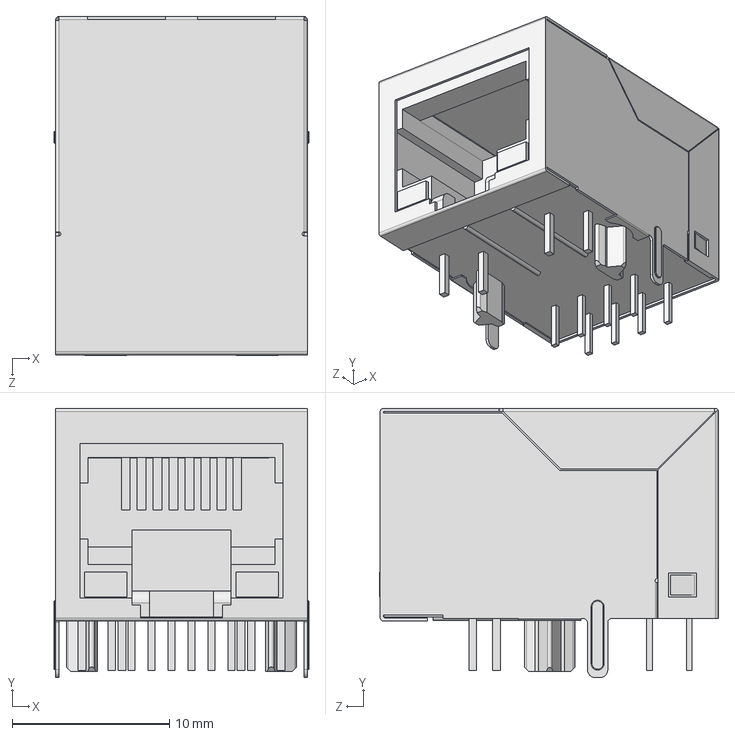
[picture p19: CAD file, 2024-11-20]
Cards/EaserCAT-7000-DIO+I2C/Kicad/Models/J0011D01BNL_3D.STEP
16.2 x 17.1 x 21.6 mm

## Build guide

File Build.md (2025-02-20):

# Building an EaserCAT board

## Parts

Most parts are generic and can be found in many places. SMD resistors and capacitors are standard, nothing special.

Crystals are standard type hc49/s.

In case of smd crystal then it's a "passive smd crystal 3225"

For ferrite beads marked BLM18EG221SN1D - you can use any generic "ferrite bead 220 Ohm 0603 1ln". Not sure if 1ln is important nor what it means. In the schematics some are called BLM18EG221SN1D, others are called BLM18EG221S. It is the same, just a mistake in the naming. 

RJ45 connectors must include "magnetics" and be configured in this way\
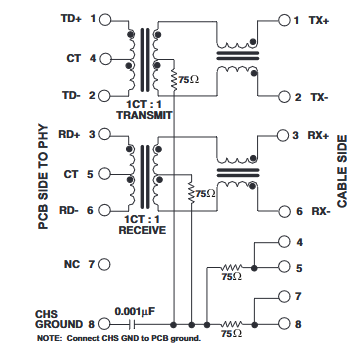
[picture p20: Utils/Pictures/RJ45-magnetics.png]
RJ45 Symbol
\
I have used PulseJack JN0011D01BNL (and most likely a chinese knockoff) and it works fine, but any jack that meets the diagram above will work.

The EtherCAT ICs are from aliexpress. There are quite a few sellers that has the LAN9252i/PT and the Ax58100 (LAN9252/PT and LAN9252V/PT are also possible, temperature range differs). Afaik, there is only one variant of the Ax58100 - AX58100LT. The LAN9252 is generally available, the Ax58100 is more of a challenge but check aliexpress.

The pcb needs to be ordered. Consider using a solder stencil - but hey it's up to you. I have bought pcbs from some chinese factories and from Aisler, Germany. The Aisler pcb is the nicest and came with excellent solder stencil. At a bit higher cost, nothing dramatic though. If you are hunting pennies then go to one of the chinese ones, maybe check prices at https://pcbshopper.com.

## EEPROM

You need to fill the EEPROM with valid contents before putting it on the pcb. It  is actually mandatory, the EtherCAT IC will not start with an empty EEPROM, or with a non-valid content. It doesn't have to be for a real EtherCAT slave, because the first thing you will do when the card works is to upload the correct contents using TwinCAT. Any valid EEPROM content.

There is a small Arduino program [Link here](Utils/EEPROM_store_valid/) that helps to fill the empty EEPROM. Follow the link.

## Populating the pcb

Enjoy!

## Soldering

I have put the pcb in the soldering oven. Hand soldering should work, although the pin spacing is only 0.4 m on the Ax58100 IC and can be a challenge. I usually get some solder bridges on the EtherCAT IC or the STM32 chip. A magnifyng device definitely helps.

## Powering up

Need:\
STLINK/V2\
Serial port - USB

Connect the STLINK/V2 unit and the serial port. The serial port will provide 5V, you don't need to see the serial output (there isn't any).

Ax58100\
Red led status - Blinking pattern means succesful read of eeprom
Gree led status - Blinking pattern indicates EtherCAT state (init, op, etc.)

LAN9252\
There is no indication.

## Hookup to TwinCAT

Install TwinCAT/XAE\
Ethernet cable\
Network interface assignment\
scan\
free-run\
download EEPROM contents

## Build and download firmware

vscode\
platformio\
open folder\
Build and upload\

## Twincat verification

## Linuxcnc

## Modifying the firmware

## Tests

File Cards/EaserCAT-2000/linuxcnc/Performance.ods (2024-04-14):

This is measured performance just after Video 10 was released. I am running the step generator on different computers, nics, kernels. This is the result
 |  |  | 1 ms | 2 ms
Jingsha H110 ITX | I210 | 4.19.302-rt131 | OK | OK
i3/7100 |  | 6.1.0-18 | NO | OK
 | r8169 | 4.19.302-rt131 | NO | OK
 |  | 6.1.0-18 | NO | OK
 | I225 | 4.19.302-rt131 |  |  | I225 not supported
 |  | 6.1.0-18 | NO | OK
Gigabyte Z170N ITX | I211 | 4.19.302-rt131 | OK | OK
i3/6100 |  | 6.1.0-18 | NO | OK
 | I219 | 4.19.302-rt131 | OK | OK
 |  | 6.1.0-18 | NO | OK
Bmax | RTL8211E | 4.19.302-rt131 | NO | OK
N4120 | r8619 driver | 6.1.0-18 | NO | OK
T8 Plus | RTL8111/8168/8411 | 4.19.302-rt131 |  |  | UHD graphics 730 not supported
N100 | r8169 | 6.1.0-18 | NO | OK

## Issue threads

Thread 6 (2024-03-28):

I2C IO?

ShadeTechnik, 2024-03-28:
Came across this whole project as I was actually in the middle of working on almost the exact same thing, then realized I wasn't the first one to have the idea which is good cuz I can't code to save my life lol.

Anyway once I get finished with my PCB I hope to be able to use this code. One thing I was curious about is if you thought about adding support for I2C IO expanders. I created a keypad a little while ago that has 4 MCP23017's that I'm eventually going to have to work into my project.....but like I said, I don't do code lol.

MetalMusings, 2024-03-29:
And I wasn't the first one either.
If you don't do code I think you will struggle with this, after the pcb is
made it is all about programming.
In the first pcb I did include connector J4 for access to the second I2C
bus, haven't used it but should be straight-forward I think.
There are many examples on how to program I2C so the function as such
should be possible.
Just keep in mind that everything works in cycles of 1 millisecond, and one
can possibly spend 300-400 microseconds doing things like checking i2c bus.
Or make it interrupt-driven in the background.

I haven't put up a video for a while now. Still stuck in step generator. It
works but not good enough, and I thought I should make it work fine first.
The PCB seems to work fine so you can take that as basis for you own design.

Den tors 28 mars 2024 kl 21:49 skrev ShadeTechnik ***@***.***
>:

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

ShadeTechnik, 2024-03-29:
Yeah it'll be a bit of a chore for me to get it going but I've got a friend that can hopefully help me out.

The PCB isn't really a concern, I'm just EtherCAT-izing an existing PCB. The one I'm currently working on is a bit more simple, it's for a control panel so it doesn't need the stepgens. From what I'm looking at so far (please correct me if I'm wrong) you used the timer based encoder peripherals. I need like 4 encoders, but much lower performance. The timer peripherals cause conflicts with other peripherals so I was just going to use an interrupt based encoder library.

Once I get this sorted out and working maybe I'll do something for higher performance encoders and stepgens, this one's hopefully going to solve some other issues I had and just get me into the world of EtherCAT. Do you have an email or some way to contact in case I have questions if you don't mind?

MetalMusings, 2024-03-30:
I think four of the timers have quadrature counting built-in and that's
what I was using. I am aiming for 100 kHz at least, that should be no
problem.
If you look in the source code I think tim1, tim2, tim5 and tim8 are
prepared for in the stm32encoder,cpp file. Those pins are fixed position
but often other pins can be moved around. On the other hand it shouldn't be
a problem to use interrupt based encoder counting.
Just be aware that if you attach an interrupt to, say, pin PB9, you can not
attach interrupts to PA9, PC9, PD9, PE9. This goes for all numbers.
And you need to handle the counter overflowing when turning many revs, but
that's kind of standard.

The interface to the LAN9252 is pretty clean. SPI(data, clock, chip
select), INT, SYNC0, SYNC1 (and RESET, but I don't think LAN9252 has that
line, the ax58100 does) are the lines you need to
work with on the MCU. Possibly make changes  for those pin numbers in the
SOES library code. Place SPI with hardware support, you want to run SPI at
40 MHz or above.

Most of the functions are not that extremely timing dependent, stepgen
stands out there. I'll try to get some time now during eastern to make it
work.

Den fre 29 mars 2024 kl 13:40 skrev ShadeTechnik ***@***.***>:

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

ShadeTechnik, 2024-03-31:
I'm actually using a smaller STM32 than you did, mine is just for a control panel and I'm using some of the GPIO from the LAN5952. I use STM32cubeIDE to check the peripherals for conflicts. I was only able to squeeze 1 timer based encoder out but that'll just be for an MPG, the others will be for like feedrate OR knobs and such so they don't demand any performance. I was able to get them all on interrupt lines without issue.

I think I managed to get my code wizard friend involved, I've asked him set me up a repo with the code arranged in a more idiotproof manner so hopefully I can follow it well enough to make necessary adjustments. He's not a machine/ethercat guy but he does do embedded programming.

I know you didn't really mention a reason for switching ESC chips but did you have some problem with the LAN9252? It's readily available and has what I need so it seems like my best bet, just curious if there's some reason I should not use it.

LAN5952 does have a nRST line. I'm debating tying it to the STM32 nRST and running them both to the same reset button.

MetalMusings, 2024-03-31:
You can't mix digital IO from the LAN9252 with MCU access using SPI. It's
either or. Check PDI MODE SELECTION, first byte in the eeprom.
One can use any MCU, not only one of the STM32s. I had it working on an
esp32 and it worked just fine, don't think I saved that "port".
It's not that much to do, mainly to get SPI working and then it works.

No I don't really have a problem with the LAN9252. I saw somewhere that
there is a bit of SPI communication overhead and that guy got
some disappointing reaction times. Not that it matters for linuxcnc. I have
had a number of issues and I sometimes suspect the LAN9252
and at one point I thought I should at least try to eliminate that factor.
So far it has turned out that LAN9252 works just fine and I haven't
come to work the AX58100 yet. Another big plus for the LAN9252 is the data
sheet. The LAN9252 has all details documented, the ax58100 does not.

Yes use one button for both, I have that on the ax58100 design. On the
LAN9252 design nRST is constant pulled-up, doesn't seem to be a problem
that it can't be reset.
I do download new code and reset the MCU regularly during development and
linuxcnc takes a few seconds pause and then its work with the new firmware.

Den sön 31 mars 2024 kl 03:02 skrev ShadeTechnik ***@***.***>:

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

ShadeTechnik, 2024-03-31:
> You can't mix digital IO from the LAN9252 with MCU access using SPI. It's either or. Check PDI MODE SELECTION, first byte in the eeprom.

This I wasn't sure about. I initially thought this but the illustration on page 10 of the the datasheet suggests this is possible "Microcontroller Mode (via SPI)" appears to show the GPIOs being active. I could not find anything that states it either way definitively but from what I gathered the GPIOs are disabled using parallel HBI or "expansion mode" as those 2 modes used the GPIO pins for either host communication or the 3rd Ethernet port. Have you actually tested this?

I haven't picked up a LAN9252 dev board to test, it's actually easier for me to just produce a prototype PCB and tinker with that so I can't test it but it would be nice to be certain that you can't do this before I bother.

MetalMusings, 2024-04-01:
You are right, it can be mixed. Didn't see that.
I wonder how that should be configured in the esi file. Are they on their
own sync managers? Maybe that is best.
Afaik SOES reads and writes the entire syncmanager contents for the RxPDO
and TxPDO. Can't have the GPIOs there.
There is an example esi file for pure Digital IO. I guess one can merge
that with an esi file for the MCU part.
Those are things that comes to mind when using the GPIOs.

Den sön 31 mars 2024 kl 16:29 skrev ShadeTechnik ***@***.***>:

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

ShadeTechnik, 2024-04-02:
Well I'm hoping my friend can sort most of that out, what I have found in the datasheet:

> 12.5 Host Interface PDI
> The value in the Extended PDI Configuration Register is used if GPIOs are enabled (SPI w/GPIO).

> 12.14.30 EXTENDED PDI CONFIGURATION REGISTER
> The bit definitions of this register are dependent on the selected PDI mode (Process Data Interface field in the PDI Control Register): Digital I/O Mode or SPI Mode.

MetalMusings, 2024-04-02:
Have a look at this MicroChip HBI+ evaluation board. It combines GPIO with
a PIC32.
I checked in the software support files. There is an esi file that at a
quick glance seems to combine GPIO with MCU data.
https://www.microchip.com/en-us/development-tool/evb-lan9252-hbiplus

Den tis 2 apr. 2024 kl 17:10 skrev ShadeTechnik ***@***.***>:

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

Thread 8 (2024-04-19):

2ms cycle time for stepgens

ShadeTechnik, 2024-04-19:
As I'm working on my own EtherCAT slave I was interested in the issue that caused the requirement for a 2ms servo thread to get the stepgens behaving correctly. I mentioned this to someone and they pointed me to a write up by Arthur Ketels where he describes some of the issues related to slaves misbehaving with distributed clocks. I'm not too familiar with this code implementation as it's not my strong suit but I'm curious if you think this could be part of your issue....

MetalMusings, 2024-04-20:
Thanks for the link, good reading.
It's like he writes, for some slaves this would pass unnoticed and it
certainly would in most other cases. But for stepper motors it is soo easy
to hear the slightest deviation in the tone.
What he mentions are things I mostly not touch. Clock synchronization,
state shifts etc is either done by the LAN9252 or by SOES and the only code
I have written is setting a flag that says I run DC.
The rest is handled by SOES.

I am more leaning towards Linux and perhaps my installation. Here is a
table I made with the linuxcnc hardware
[image: bild.png]
So I can get reliable 1 ms cycle times under some conditions.
I ran this off the same USB SD-card installation. That can be source of the
problem of course, it eliminates some other problems.
The only thing I didn't check is the frequency of the LAN9252 crystal. I
better do that.

How are things going btw?

Den fre 19 apr. 2024 kl 04:10 skrev ShadeTechnik ***@***.***>:

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

ShadeTechnik, 2024-04-20:
It's hard to understand where the issue is actually coming from, or actually what the issue is. Are you able to run a Mesa card @ 1ms servo thread on the same system? You would think if there are no problems running a Mesa card that the PC itself would be capable of handling an EtherCAT slave @ 1ms as well. Most of my systems are mobile CPUs on miniPCs with Realtek NICs and aside from bios issues I've always been able to manage 1ms with a Mesa card.

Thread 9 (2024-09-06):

May I ask how I should configure the HAL file

84864797, 2024-09-06:
Hello
May I ask how I should configure the HAL file
For example, I want to use PE9~PE15 on stm32f407
How should I write it in the HAL file

MetalMusings, 2024-09-06:
When you have made your Ethercat device, follow examples from here https://github.com/linuxcnc-ethercat/linuxcnc-ethercat

84864797, 2024-09-06:
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

Hello
Which pin on the MCU corresponds to the enc-pos-scale? Where can I find it

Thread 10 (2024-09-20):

Hello Can you explain the functions of these sockets on EaserCAT 2000?

84864797, 2024-09-20:
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

Hello
Can you explain the functions of these sockets on EaserCAT 2000?

MetalMusings, 2024-09-20:
There are no pre-determined functions for these sockets. I made as many
sockets as I could and
tried to have the pins assigned so some sockets could use the hardware
encoder counter,
some sockets could use the PWM timer. It really depends on the code that is
used in the STM32,
and I never finished that part.

Den fre 20 sep. 2024 kl 11:38 skrev 84864797 ***@***.***>:

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

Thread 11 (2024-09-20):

LAN9252 core board

84864797, 2024-09-20:
Hello
May I ask a question
LAN9252 comes with 16 GPIO built-in, and I can run the LAN9252 core board using the Dig_8IN_8OUT.xml file you provided.
I want to configure it with 12 digital inputs and 4 digital outputs, but I tried for 2 days but couldn't succeed. I have no choice but to seek your advice

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

MetalMusings, 2024-09-20:
Hi,
this is a setting in the eeprom. The byte to change is the one below
[image: bild.png]
It determines if a pair of i/os are inputs or outputs.
It's the Extended PDI Configuration Register.
See section 12.14.30 in
http://ww1.microchip.com/downloads/en/devicedoc/00001909a.pdf
You can find details on the eeprom contents in section 12.8 in the same
document.
There is no way around reading the datasheet for these kind of details.

Change the value above, and upload the new firmware to LAN9252 in Twincat.
You might need to change the "bitlen" field in the pdos above in the xml
file.
Hope it works.

Den fre 20 sep. 2024 kl 11:47 skrev 84864797 ***@***.***>:

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

84864797, 2024-09-20:
Thank you for your response
Where are these values modified? Is it SSC?

MetalMusings, 2024-09-20:
At the end of the Dig_8IN_8OUT.xml file. Change it with a normal text
editor.

Den fre 20 sep. 2024 kl 16:35 skrev 84864797 ***@***.***>:

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

84864797, 2024-09-20:
`<EtherCATInfo xmlns:xsi="http://www.w3.org/2001/XMLSchema-instance" xsi:noNamespaceSchemaLocation="EtherCATInfo.xsd" Version="1.6">
<Vendor>
<Id>#x000004D8</Id>
<Name>Microchip Technology Inc</Name>
</Vendor>
<Descriptions>
<Groups>
<Group>
<Type>LAN9252-DIGIO</Type>
<Name LcId="1033">LAN9252-DIGIO</Name>
<ImageData16x14>424DD8020000000000003600000028000000100000000E0000000100180000000000A2020000120B0000120B000000000000000000001306E31306E3190CE42B1FE62B1FE61306E31F13E5190CE42519E51306E31306E3190CE42F24E7190CE41306E31306E31306E31306E35F56EC645CED645CED4137E91F13E5473DE95F57EC3227E71306E3473DE95A51EC271BE61306E31306E31409CA524CC68E8AD74F48C1615CC82218D03E36BF716BCE746FCE453DC01307CE3931BA7D78D27671D1150CB21409CA1712801B1D1D1B1D1D1B1D1D1B1D1D120B891B1D1D1B1D1D1B1D1D1B1D1D120B891B1D1D1B1D1D1B1D1D1B1D1D1712801712807F8080D4D5D5D4D5D5383939120B89545656D4D5D5D4D5D5626464130C89292B2BD4D5D5D4D5D56264641915801712804647471B1D1DAAAAAAD4D5D5130E82383939292B2B717272D4D5D5151183D4D5D57F80801B1D1D7172721E1C81191580464747D4D5D5D4D5D51B1D1D19158A292B2BD4D5D5D4D5D5292B2B1B1B8AD4D5D56264641B1D1D1B1D1D2427821E1D81D4D5D54647476264643839391E208BD4D5D57F8080464747545656242A8BD4D5D59B9C9C292B2BAAAAAA2D3683252882464747D4D5D5D4D5D51B1D1D272D85292B2BD4D5D5D4D5D5292B2B2E37861B1D1DD4D5D5D4D5D5464747394484323BB52324812122822426822526824554C0323883292B822A2D83353C84424CBF3238843940842E32834853865D6EBB5262EB3E43E83334E74147E94349E9535FEB4D56EA5662EB484DEA545DEB636FED545AEA5A63EC6671ED8CA0F290A5F2748AEF6B7BEE5D68EC6874ED788AEF8397F17684EF7986EF8C9FF2818FF1818EF08E9DF18A97F18791F19BA9F3B0C0F691A4F291A2F28390F192A1F29CACF3A3B3F498A6F3A4B3F4AEBDF5B0BEF59EA8F3A3ADF4BBC7F7C4D1F8CAD7F8CED9F9B4C4F6B8C8F6ACB8F59AA3F3B6C1F6C5D2F8C2CDF8CCD7F9D2DDF9D5E0FAD2DAF9D5DCF9DFE7FBE2E9FBE5EBFBE8EEFB0000</ImageData16x14>
</Group>
</Groups>
<Devices>
<Device Physics="YY">
<Type ProductCode="#x0000000d" RevisionNo="#x00000001">LAN9252-DIGIO-2PORT</Type>
<Name LcId="1033">
<![CDATA[ 9252 8 Ch. Dig. In-/Output 2xMII (No DC) ]]>
</Name>
<Info>
<EtherCATController>
<DpramSize>4096</DpramSize>
<SmCount>4</SmCount>
<FmmuCount>3</FmmuCount>
</EtherCATController>
<Port>
<Type>MII</Type>
<PhysicalPhyAddr>0</PhysicalPhyAddr>
</Port>
<Port>
<Type>MII</Type>
<PhysicalPhyAddr>1</PhysicalPhyAddr>
</Port>
<IdentificationAdo>#x0012</IdentificationAdo>
</Info>
<GroupType>LAN9252-DIGIO</GroupType>
<Fmmu>Outputs</Fmmu>
<Fmmu>Inputs</Fmmu>
<Sm StartAddress="#x0f01" ControlByte="#x44" Enable="1" OpOnly="1">Outputs</Sm>
<Sm StartAddress="#x1000" ControlByte="0" Enable="1">Inputs</Sm>
<RxPdo Fixed="1" Sm="0">
<Index>#x1a00</Index>
<Name>Byte 0</Name>
<Entry>
<Index>#x3101</Index>
<SubIndex>1</SubIndex>
<BitLen>8</BitLen>
<Name>Output</Name>
<DataType>BITARR8</DataType>
</Entry>
</RxPdo>
<TxPdo Fixed="1" Sm="1">
<Index>#x1600</Index>
<Name>Byte 0</Name>
<Entry>
<Index>#x3001</Index>
<SubIndex>1</SubIndex>
<BitLen>8</BitLen>
<Name>Input</Name>
<DataType>BITARR8</DataType>
</Entry>
</TxPdo>
<Eeprom>
<ByteSize>2048</ByteSize>
<ConfigData>040F00441027F0FF</ConfigData>
</Eeprom>
</Device>
</Devices>
</Descriptions>
</EtherCATInfo>`

抱歉 我对这些知识一窍不通，您能说的清楚一点吗  怎么对0152h-0153h 里面的内容进行更改？

XML文件的末尾应该怎么编写

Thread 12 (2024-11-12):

EaserCAT 3000

cofhal, 2024-11-12:
From what I have read and in the files there is no information on programming this new card. There is no code for the eeprom.
There are no LINUXCNC configuration examples for this card nor XML files to use it.

MetalMusings, 2024-11-13:
That's right. It was never completed. I didn't get the Ax58100 to connect
to TwinCAT ethercat master.
So I have gone back to LAN9252. The problem with Ax58100 is the poor
documentation, it doesn't give enough detail.
And then it is more or less hopeless to get it debugged when it doesn't
start.

If you are interested to use the Ax58100 here are some tips
EEprom programming is done the same as for the LAN9252, with
EEPROM_generator. Make sure the EEPROM config_data is correct for the
Ax68100 (end of generated xml file). And that can be a problem. I haven't
found a description of the field. There are some examples in the Ax58100
data download area one can use.
After you get it going with TwinCAT you can program it just like the
previous card. Set it up for linuxcnc like any other Ethercat card
But I recommend you use LAN9252 instead.

Den tis 12 nov. 2024 kl 23:00 skrev Francisco J. Hoyos <
***@***.***>:

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

cofhal, 2024-11-13:
Too bad I had one of those cards assembled. I'll have to use it as a paperweight.

cofhal, 2024-11-13:
Thank you for your support. I have very little experience with this topic. Have you checked this project or where they use this IC?

https://github.com/kubabuda/ecat_servo/tree/main

cofhal, 2024-11-14:
I understand, I have another question, do I finish the firmware for the STM32F407VGT6 of that card or not?

cofhal, 2024-11-14:
What was the function you were looking to have from this board?
I just wanted to experiment, I already have some servo drivers with ethercat and also several MESA cards and I wanted to investigate more about Ethercat and I found your project.
I'm interested because it could be used on a 4-axis milling machine,

MetalMusings, 2024-11-15:
You know what? I soldered up another board. And, it works as far as it will
read the EEPROM and lit up the EEPROM_DONE led.
I now actually thinks this might work after all.

I went through the design yesterday and compared to ax58100 evaluation
board schematics. Apart from perhaps two resistor's values, it should be ok.
Anyways, later today I will solder on the network connector and test it
with Twincat. There is a good chance it will work, I think.

Den tors 14 nov. 2024 kl 20:34 skrev Francisco J. Hoyos <
***@***.***>:

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

MetalMusings, 2024-11-15:
YES! It works! I am quite happy with that.
I have a blinking RUN_LED which means the Ax58100 has entered EtherCAT Init
state.
I ask it to go to OP state and yes it does it.
That changes things. It works.

I will do some further tests myself. I have really wondered what was wrong
with it.
It seems I didn't build it properly.

So, do you want to make it work? You should start by programming an EEPROM
and solder in place.
It will not start without a valid eeprom. It can be any valid contents,
doesn't matter.
When it is up in TwinCAT it can easily be reprogrammed from there.

Den fre 15 nov. 2024 kl 09:21 skrev Håkan Båstedt ***@***.***>:

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

cofhal, 2024-11-15:
I'm glad it worked. From what I understand, it's not possible to program the EEPROM from the card, which seems strange to me. According to that, I have to unsolder it and do the programming outside the card. Regarding programming, I'm still reading and researching how to do it, I don't really know how to do it.

MetalMusings, 2024-11-15:
The very first time it needs to be programmed from outside. After that it
can be reprogrammed with TwinCAT or a SOES uitility.
Programming is done by the Ethercat chip, so ethercat must be running, and
it won't start with a bad eeprom content. First time.

 Easiest is to connect the eeprom to an arduino (I used an esp32), there
are several guides, here is one.
https://sonyarouje.com/2016/04/14/connect-arduino-to-external-eeprom/
I can send you an Arduino sketch that programs with the right contents.

Den fre 15 nov. 2024 kl 15:20 skrev Francisco J. Hoyos <
***@***.***>:

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

MetalMusings, 2024-11-15:
Arduino sketch to program the eeprom. Works for both AX58100 and LAN9252.
Comment out line 9 if you only want to read the content.
Install I2C_eeprom arduino library.

Den fre 15 nov. 2024 kl 15:34 skrev Håkan Båstedt ***@***.***>:

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

cofhal, 2024-11-15:
Thank you very much for your support, please send me that to do the EEPROM programming.

MetalMusings, 2024-11-15:
I hope here
[LAN9252-eeprom-store-valid.txt](https://github.com/user-attachments/files/17777046/LAN9252-eeprom-store-valid.txt)
Rename from txt to ino

cofhal, 2024-11-15:
Thanks, I have another question: if I want to program the EEPROM for the AX58100 should I delete the part of the .ino file where the content for the LAN 9252 is?

MetalMusings, 2024-11-16:
Not needed, it should work as is. Make sure the three lines are like this
```
//#define LAN9252
#define AX58100
#define PROGRAM_EEPROM
```

MetalMusings, 2024-11-16:
I have now verified that the STM32 and the Ax58100 works fine over SPI. Replicated a EtherCAT client using LAN9252.
They are now more or less interchangeable.
I mentioned a problem with the reset circuit before. Yes, there is a bug on the board. You should add a wire as in the picture. It's on the outermost pin on the STM32F407. It can be any digital IO pin, this one is particularly easy to solder a wire to.
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
Apart from that EtherCAT and SOES seems to work just fine.

cofhal, 2024-11-16:
Fantastic, I'm glad everything is working for you and that you haven't given up. I'm waiting for an STM32 board to arrive so I can program the EEPROM, I only have Arduinos and the file you sent me doesn't work for them.

cofhal, 2024-11-17:
Yes, but some instructions only work with STM32 cards, I tried to compile your code for an Arduino Nano and it always gives an error, while if I compile for an SMT32 card it compiles without errors.

MetalMusings, 2024-11-17:
I see, it is the Serial.printf() function. Well, it is easy to get used to that one.
It is only for the printout, not the actual programming.
I have a modified version here.
[LAN9252-eeprom-store-valid.txt](https://github.com/user-attachments/files/17790387/LAN9252-eeprom-store-valid.txt)

cofhal, 2024-11-18:
I tried to program the EEPROM with the new file, it compiles correctly but this error always appears on the console:
I70:0000000000
80:00000000FFFF
90:000000FFFFFFFF
100:FFFFFFFFFFFFFFFFFFFF
110:FFFFFFFFFFFFFFFFFFFFFF
120:00001F0106967
130:6974616C2031362D496E
140:7075742F31362D4F7574
150:707574291E042202844
160:0200000000
1 70:00101100000
180:000000FFFF100
190:101012290C0
200:2F00440133F
210:0044013FFFF00
220:00280FFFFFFFFFFFF
230:FFFFFFFFFFFFFFFFFFFF
240:FFFFFFFFFFFFFFFFFF010
250:000014FFFF
-----------------------------------
I think it is writing to the EEPROM but I'm not sure.

MetalMusings, 2024-11-19:
It fails

> Failed writeBlockVerify

it will say when succesful

> That's it. It worked

The numbers below are read from the eeprom and should be the same as written

> unsigned char eeprom_data[] = {
>   0x04, 0x0d, 0x00, 0x44, 0x10, 0x27, 0x00, 0xff, 0x00, 0x00,
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
TC227, 2024-11-21:
<masters>
  <master idx="0" appTimePeriod="1000000" refClockSyncCycles="5">
    <slave idx="0" type="generic" vid="0x00000b95" pid="0x00610300" configPdos="true">
      <dcConf assignActivate="300" sync0Cycle="*1" sync0Shift="0"/>

      <syncManager idx="2" dir="out">
        <pdo idx="1600">
          <pdoEntry idx="7000" subIdx="00" bitLen="32" halPin="enc-pos-scale" halType="s32"/>
        </pdo>
        <pdo idx="1601">
          <pdoEntry idx="7001" subIdx="00" bitLen="32" halPin="enc-index-latch-enable" halType="u32"/>
        </pdo>
        <pdo idx="1602">
          <pdoEntry idx="7002" subIdx="01" bitLen="64" halPin="commanded-position" halType="float-double"/>
        </pdo>
      </syncManager>

TC227, 2024-11-21:
<masters>
  <master idx="0" appTimePeriod="1000000" refClockSyncCycles="5">
    <slave idx="0" type="generic" vid="0x00000b95" pid="0x00610300" configPdos="true">
      <dcConf assignActivate="300" sync0Cycle="*1" sync0Shift="0"/>

      <syncManager idx="2" dir="out">
        <pdo idx="1600">
          <pdoEntry idx="7000" subIdx="00" bitLen="32" halPin="enc-pos-scale" halType="s32"/>
        </pdo>
        <pdo idx="1601">
          <pdoEntry idx="7001" subIdx="00" bitLen="32" halPin="enc-index-latch-enable" halType="u32"/>
        </pdo>
        <pdo idx="1602">
          <pdoEntry idx="7002" subIdx="01" bitLen="64" halPin="commanded-position" halType="float-double"/>
        </pdo>
      </syncManager>

      <syncManager idx="3" dir="in">
        <pdo idx="1a00">
          <pdoEntry idx="6000" subIdx="00" bitLen="64" halPin="enc-position" halType="float-double"/>
        </pdo>
        <pdo idx="1a01">
          <pdoEntry idx="6001" subIdx="00" bitLen="64" halPin="enc-frequency" halType="float-double"/>
        </pdo>
        <pdo idx="1a02">
          <pdoEntry idx="6002" subIdx="00" bitLen="32" halPin="DiffT" halType="u32"/>
        </pdo>
        <pdo idx="1a03">
          <pdoEntry idx="6003" subIdx="00" bitLen="32" halPin="index-byte" halType="u32"/>
        </pdo>
        <pdo idx="1a04">
          <pdoEntry idx="6004" subIdx="00" bitLen="32" halPin="index-status" halType="u32"/>
        </pdo>
        <pdo idx="1a05">
          <pdoEntry idx="6005" subIdx="01" bitLen="64" halPin="actual-position" halType="float-double"/>
        </pdo>
      </syncManager>
    </slave>
  </master>
</masters>

MetalMusings, 2024-11-21:
Tips is to search in the source to lcec https://github.com/linuxcnc-ethercat/linuxcnc-ethercat
It think the "double" data-type got renamed by Scott to "float-double-ieee"
Try that instead of "float-double".

MetalMusings, 2024-11-21:
Didn't it work with lcec-configgen? That would be the best place to start,

cofhal, 2024-11-21:
I don't know what I'm doing wrong but TWINCAT doesn't detect the card, and I really don't know what to do to make it work. I've never used that program.
I tried to compile the firmware, it starts compiling it but the problem is that there is an error.
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

cofhal, 2024-11-21:
The funny thing is that if I try to compare it with VSC in Linux it also ends with an error but differently.
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

MetalMusings, 2024-11-21:
Watch three minutes of this video, maybe there is step you miss or something you see
https://youtu.be/IGmXsXSSA4s?t=396  (from 6:30)

The compiler is for ARM in the first screenshot. That's not right.
Maybe best to do a reset on the software and you use the version from github. It is easier for me to upload and fix.
`% git clone https://github.com/MetalMusings/MyOwnEtherCATDevice`
Oooh I see. Someone wrote MyENcoder.h instead of MyEncoder.h and didn't check it. N vs n. I fixed it.

So it seems building and so works ok under linux. Maybe you should install Platformio ST STM32 platform on Windows, check in the platformio/install menue. I develop mostly in Windows.

TC227, 2024-11-22:
Twincat may have problems if not using Intel LAN card.

TC227, 2024-11-22:
> Didn't it work with lcec-configgen? That would be the best place to start,

I will study it seriously again.

TC227, 2024-11-22:
I changed halType="float-double-ieee" but still stuck here.
Pin 'lcec.0.0.cia-statusword' does not exist
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

MetalMusings, 2024-11-22:
You have to understand what is going on now. You have taken a linuxcnc config for a different EtherCAT card.
That will not work. You have to match the linuxcnc config with the EtherCAT card and use the pins that you just defined in the ethercat-conf.xml.

TC227, 2024-11-22:
OK
I'll start over with this.
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

TC227, 2024-11-22:
At this time, I think the system is ready to be OP.
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

MetalMusings, 2024-11-22:
I guess it is already in OP if you can show such a picture.
For the cia402 issue. Remove the cia402 component, it is not a cia402
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

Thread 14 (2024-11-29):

EaserCAT-3000  PWM OUTPUT

TC227, 2024-11-29:
I'm trying to find the command component ///// Analog out
const byte DAC1_pin = PA4; to use as a spindle. I'm going to add an Op-amp
But I'm not sure if there's a command to generate PWM.

MetalMusings, 2024-11-29:
It is Arduino platform so it is a basic analogWrite() command.
Bear in mind the pin output is only 0-3.3V so you may need additional circuitry to get +-10V

TC227, 2024-11-30:
Do I need to enable it?
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

////// EtherCAT routines called regularly, to read data, do stuff and write data
void cb_set_outputs(void) // Get Master outputs, slave inputs, first operation
{
   for (int i = 0; i < min(sizeof(Obj.Outputs), sizeof(OUTPUTS)); i++)
      digitalWrite(OUTPUTS[i], Obj.Outputs[i] == 1 ? HIGH : LOW);
   // analogWrite(DAC1_pin, Obj.Voltage);
   // Encoder1.setLatch(Obj.IndexLatchEnable);
   // Encoder1.setScale(2000);

TC227, 2024-11-30:
I edited main.cpp to link esi
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

and edited EEPROM generator to create soes-esi
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

compiled and uploaded eeprom via twincat with newly added XML and it's done
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

but twincat still doesn't find link to 6007 Voltage and 7010 IndexLatchEnable
what else do I need to change

MetalMusings, 2024-11-30:
EEprom update
MCU update
ethercat-conf.xml update
hal update
all needs to be updated. For Twincat the eeprom and mcu needs to be updated.

TC227, 2024-11-30:
Yes, it's funny that I forgot to update the MCU now that I've found it in LCNC.

MetalMusings, 2024-11-30:
When using with a MCU, sometimes it is the content in the eeprom, sometimes the MCU's data model that are needed. Best to update both.

TC227, 2024-11-30:
TWINCAT OK
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

MetalMusings, 2024-11-30:
There it is. But Voltage is an input. Don't you want that as an output?

TC227, 2024-11-30:
I'm still confused, does the DAC voltage have to be moved to the output? And should the index be the input?

TC227, 2024-11-30:
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

MetalMusings, 2024-11-30:
If you want to set a voltage or pwm duty cycle on the DAC pin, it should be set as output.
The terminology can be confusing. When doing the eeprom and looking at the soes code, input and output is from the Ethercat master's perspective.  Not from the client's. So yes it should be set as output.
Regarding inputs 1/0, start in twincat. See if it reacts when you set the pin high(3.3V) or low (gnd). If that works, do the same in linuxcnc. It can be anything from the hardware, collision with other functions like timers, or the setup.

TC227, 2024-12-01:
Thanks for the advice, now I can control 0-3.3V at PA4, when I test 255 it outputs 3.3V.
I am now building the next OP-AMP, I will start experimenting with LM358.

MetalMusings, 2024-12-01:
You can check out here to get more steps than 255, if you need that. Never tested myself.
https://www.stm32duino.com/viewtopic.php?t=1105

DesertShedStudio, 2024-12-05:
@TC227 For a 3.3v spindle DAC circuit, you may find Peter's post here useful (Mesa 7i76 Spindle DAC Schematic)
[https://forum.linuxcnc.org/39-pncconf/33991-configuration-7i92m-7i76x1d?start=40#110131](url)

TC227, 2024-12-05:
Wow, that's right. So glad. I was looking for this post a few days ago but couldn't find it. I had a bad experience connecting +15 -15 which combined to 30V. I later found out that it should be 7.5+7.5 or 10+10. It damaged my 7i96 at 4001 and 4218. I still haven't fixed it to work.

Thanks for helping me.

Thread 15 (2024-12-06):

EaserCAT-4000

DesertShedStudio, 2024-12-06:
I believe the .kicad_pcb and .kicad_pro files are missing from the EaserCAT-4000-THCAD-Reader Kicad subfolder.

MetalMusings, 2024-12-06:
Should be fixed now. Was a bad .gitignore

DesertShedStudio, 2024-12-06:
Awesome, Thank you !

Closed 2024-12-06.

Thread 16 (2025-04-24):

Using Two THTIC Boards with EASERCAT-7000-DIO+I2C – Are Both I2C Inputs Designed for That?

Smith3rman, 2025-04-24:
Hi,

I'm working on a LinuxCNC-based plasma setup and considering using two THTIC boards for material sensing – one for arc voltage monitoring and the other for ohmic/hypersensing.

The EASERCAT-7000-DIO+I2C has two I2C inputs, and I'm wondering if it was part of the original design to support dual THTICs simultaneously via I2C. If so:

Are there any specific considerations regarding voltage scaling (e.g., resistor values or divider networks) when using one THTIC for ohmic sensing?

In particular, would it be beneficial to adjust the voltage scaling components for better resolution, or do you think the existing range (up to ~200V) with the limited ADC resolution is still accurate enough for reliable hypersensing?

The idea is similar to what's described in this [LinuxCNC forum thread on hypersensing](https://forum.linuxcnc.org/plasma-laser/37311-hypersensing-with-thcad-better-way-to-do-ohmic-sensing?start=0), where precise detection of voltage rise is used to sense material contact without relays or diodes.

Any guidance or clarification would be super helpful, especially if this setup was already anticipated in the hardware/firmware design. Thanks for your time and for making this open-source!

Best regards,
Smith3rman

MetalMusings, 2025-04-24:
It's not part of the design, but it can easily be done.
- I2C devices are connected in series, the I2C port on the E7000 is fine, no hardware changes needed.
- Use different I2C addresses for the ADCs. Depends on which ADC you use how that is done.
- Modify the firmware (quite easy, mostly cut and paste) to support multiple units.
- Add PDOs (and SDOs) for the second (and third etc) I2C device.
The limiting factor would be the data read time from the I2C devices, each somewhere 100 usecs, so a few can be had but not ten.

The voltage divider should give around 2 V to the ADC when cutting (arc voltage around 100V). The ADC has a range of 0-4V (0-5V) and one wants to be somewhere in the middle.
I adjusted resistor values after my plasma cutter that gives out full arc voltage. If your arc voltage is already scaled down, adjust resistors to give 2V at cutting voltage. You can also double-check power dissipation from the resistors, that's the reason for those high 100's kOhm resistor values. Also finding resistors that can handle 500V or so, one need to go with the larger size. If you have say 5V out, you can use a few kOhm 0805s.

Don't know or don't understand the difference for hypersensing. The ADCs are quite sensitive in this config, 11 or 12 bit resolution already. The only risk I can think of is to have too high voltage on the ADC input. There are limits, around 6V as max. I have placed a zener diode in an attempt to bleed off any voltage higher than the zener diode value. But not really tested. If that works reliably, you can adjust resistors to a smaller range maybe 0-30V (I don't know as I said) and let the zener diode bleed off the high voltages when cutting. If that's beneficial for ohmic sensing.

I would think that the THTIC combo with E7000 certainly is quick enough and have the precision needed. I have used it for many hours in my own setup and it works great. It just works.

Smith3rman, 2025-04-24:
Thanks a lot for the thorough explanation!

That clears things up really well — great to know that using multiple THTICs over I2C is totally doable with just different I2C addresses and a small firmware tweak. It’s also good to hear the E7000 handles this setup with no hardware mods needed.

Just to add to the context:
I think what’s often referred to as “ohmic sensing” is the more basic method using voltage detection through opto-isolated relays — basically a digital signal indicating contact. In contrast, what I understood as “hypersensing” (like described [here](https://forum.linuxcnc.org/plasma-laser/37311-hypersensing-with-thcad-better-way-to-do-ohmic-sensing?start=0)) uses continuous voltage monitoring to detect the ramp-up as the torch touches the material. This method, especially with ohmic.comp in LinuxCNC, allows setting both an upper and lower threshold for strong hysteresis, making it much more robust and noise-resistant.

With the 12-bit ADC, even when scaled for ~100V arc voltage, the resolution should still be totally fine for detecting the ramp-up and touch event accurately — so no changes needed to the scaling for this use case. Only customization needed is the firmware support for multiple I2C addresses — and since I only need two, that fits perfectly.

Thanks again — really appreciate the help and the great work on this project!

MetalMusings, 2025-04-24:
Isn't it just to add a power source and measure with the existing Arc Voltage reader?

From one of the schematics.
There is already an isolated power supply, let's add one more 24V. And bring to a regulated voltage.
One would need to know when to activate the power supply and when not to, but there seems to be an Ohmic Sensing output pin one can use.

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

Smith3rman, 2025-04-24:
Yes, I think you're absolutely right — if the plasma voltage wont destruct the Voltage regulator U6-LM7815, but i think in this case even after the 300k resistor there is a high possibility that the unisolated regulator may break, i think in the datasheet there is even mentioned that there shouldnt be a feedbackward voltage.

Adding another isolated 24V power source, which is isolated and regulated in one part makes perfect sense, especially since the rest of the ADC path is already isolated and protected.
A solution for the isolation part would be this part: https://recom-power.com/en/products/dc-dc-converters/dc-dc-converters-regulated/rec-p-RSH2-0524S!sH2.html?4
And as you mentioned, using the Ohmic Sensing output pin as a control signal for enabling the power source seems like a clean and logical approach, but i think in that case it was mentioned because of one of the mesa boards they used but i think i can easily use one of the output pins of the Easercat 7000.

MetalMusings, 2025-04-25:
Was a quick hack there with the schematics.
So how to connect/disconnect? A small relay could work. Nothing is time critical with that. Can control the relay with an I2C IO expander. Then everything is on the TIC board (new design), controlled with I2C from E7000. Or bring in an extra output signal from the E7000.
The DC-DC converter you link to has only 50 mV p-p max ripple. I have seen worse. Maybe that is good enough so one don't need the voltage regulator at all?
Unfortunately my plasma cutter is one of those where the torch shield is already connected to ground so I can not immediately use this method. I need to disconnect the shield and work piece during piercing and I can do that with a 200A contactor for the work piece current. Or unknown current if disconnecting the torch ground, for the blowback start. Just guessing that ground current is less. I don't want to make modifications to the plasma cutter, staying on the outside.

Smith3rman, 2025-04-25:
Yeah thats why i send that Dc Converter here, it also has an integrated I/O for switching On/off i think, so in total a good  fit. I think i will try it, but it will take sometime. I ordererd the PCBs yesterday 😄 and also i need to buy the parts, so some time will go down the river....
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
Smith3rman, 2025-05-17:
Is there a way to only generate a bin-file for the LAN9252 over [https://kubabuda.github.io/EEPROM_generator/](EEprom Generator) directly, because its showing up at the bottom a possibility to download the HEX file directly. I’m using a USB programmer that supports writing directly to EEPROMs from .bin files, so if I configure all values correctly, I’d prefer to write the binary file directly from that. I did only change there the Number of bytes in EEPROM item and the ESC, in my flasher its still showing up that file length is larger than chip capacity....

And with Ohmic sensing is really nice! Which parts did you implement?

MetalMusings, 2025-05-17:
I think I misunderstood you there, you are asking for the first initial eeprom write I guess.
If you have a better way then arduino then by all means use that.
It might be that the bin file from eeprom_generator will work for that initial write. I am almost 99% sure about that.
But it won't give you all the PDOs and SDOs, for that you need to go through TwinCAT and the esi file when it is up and running.

Ohmic sensing - a car relay and the 24v-24v dc converter you pointed to, not exactly the same since it was difficult to source but a through-hole version.

Smith3rman, 2025-06-18:
Really nice work with the Ohmic Sensing!
I did now populate the PCB and one of The THTIC and flashed The Eeprom and the STM.
Next step is the Twincat Step!

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

Smith3rman, 2025-06-18:
The power supply is already working only thing which is a little fishy is that the green led on the STM is getting like 1,7V the whole time

Smith3rman, 2025-06-19:
So in the IDE the STM showed up as I flashed, I did not change the programming yet, but D25 flashed since beginning a little.

MetalMusings, 2025-06-19:
Here is the code snippet in main.cpp. D25 is PB4 (have to schematics)
```c
void setup(void)
{
   Serial1.begin(115200);

   for (int i = 0; i < sizeof(inputPin); i++)
      pinMode(inputPin[i], INPUT_PULLDOWN);
   for (int i = 0; i < sizeof(outputPin); i++)
   {
      pinMode(outputPin[i], OUTPUT);
      digitalWrite(outputPin[i], LOW);
   }
   // Debug leds
   pinMode(PB4, OUTPUT);
   pinMode(PB5, OUTPUT);
   pinMode(PB6, OUTPUT);
   pinMode(PB7, OUTPUT);
   digitalWrite(PB4, LOW);
   digitalWrite(PB5, LOW);
   digitalWrite(PB6, LOW);
   digitalWrite(PB7, LOW);

```
You can, as a test, set it or any of them to high, to verify that the STM is working.

MetalMusings, 2025-06-21:
Just want to mention that it isn't necessary to use TwinCAT for the eeprom content.
The sii_tool can take an xml-file and make the content of the eeprom
`sii_tool -m < esi.xml > eeprom.bin`
https://github.com/synapticon/siitool

Write to the device with
`ethercat sii_write -p <n> eeprom.bin`

The new (for me) is the -m flag that makes all the difference.

Smith3rman, 2025-06-25:
So I got it to work, the LED was only floating, because the Pin wasn't programmed. The Ic works. Are there any specific things I need to do with the Siitool or is there a good description?

Smith3rman, 2025-06-25:
That was my question if you had already done the ESI file or if I needed to set it up new 👍

MetalMusings, 2025-06-25:
The esi file in Firmware/lib/soes-esi works.

MetalMusings, 2025-06-25:
I used it on my linuxcnc pc. I stopped linuxcnc, did the programming and then tried with linuxcnc.

Smith3rman, 2025-06-25:
What I forgot to ask was if you got a seeable difference in the cut with the hypersensing?

Smith3rman, 2025-07-11:
So i am right now facing some problems with the upload over the ESP32 to the Eeprom i tried it but it seems to not work correctly. Its showing up that its programming the eeprom but if monitor it, it shows that it only uploads zeros. I did connect everything right, but i dont next step

Smith3rman, 2025-07-11:
So I faced some issues with initial flashing of the Eeprom of Lan9252 so I unsoldered it and tried to reprogram it with esp32

Smith3rman, 2025-07-11:
There is a testcode to check device address and verify it to be 0x50 but it never gets detected

MetalMusings, 2025-07-11:
EEPROM_store_valid ?
Schematics here https://github.com/RobTillaart/I2C_EEPROM#schematic
I can not find my little programmer board now, but I have it connected just like that, and to the standard I2C pins on the esp32.
Try with another eeprom? Try different addresses 50-57?

MetalMusings, 2025-08-04:
You are busy :)
Also got it working?
That's my favorite card, it has seen many hours of use in my plasma cutter.

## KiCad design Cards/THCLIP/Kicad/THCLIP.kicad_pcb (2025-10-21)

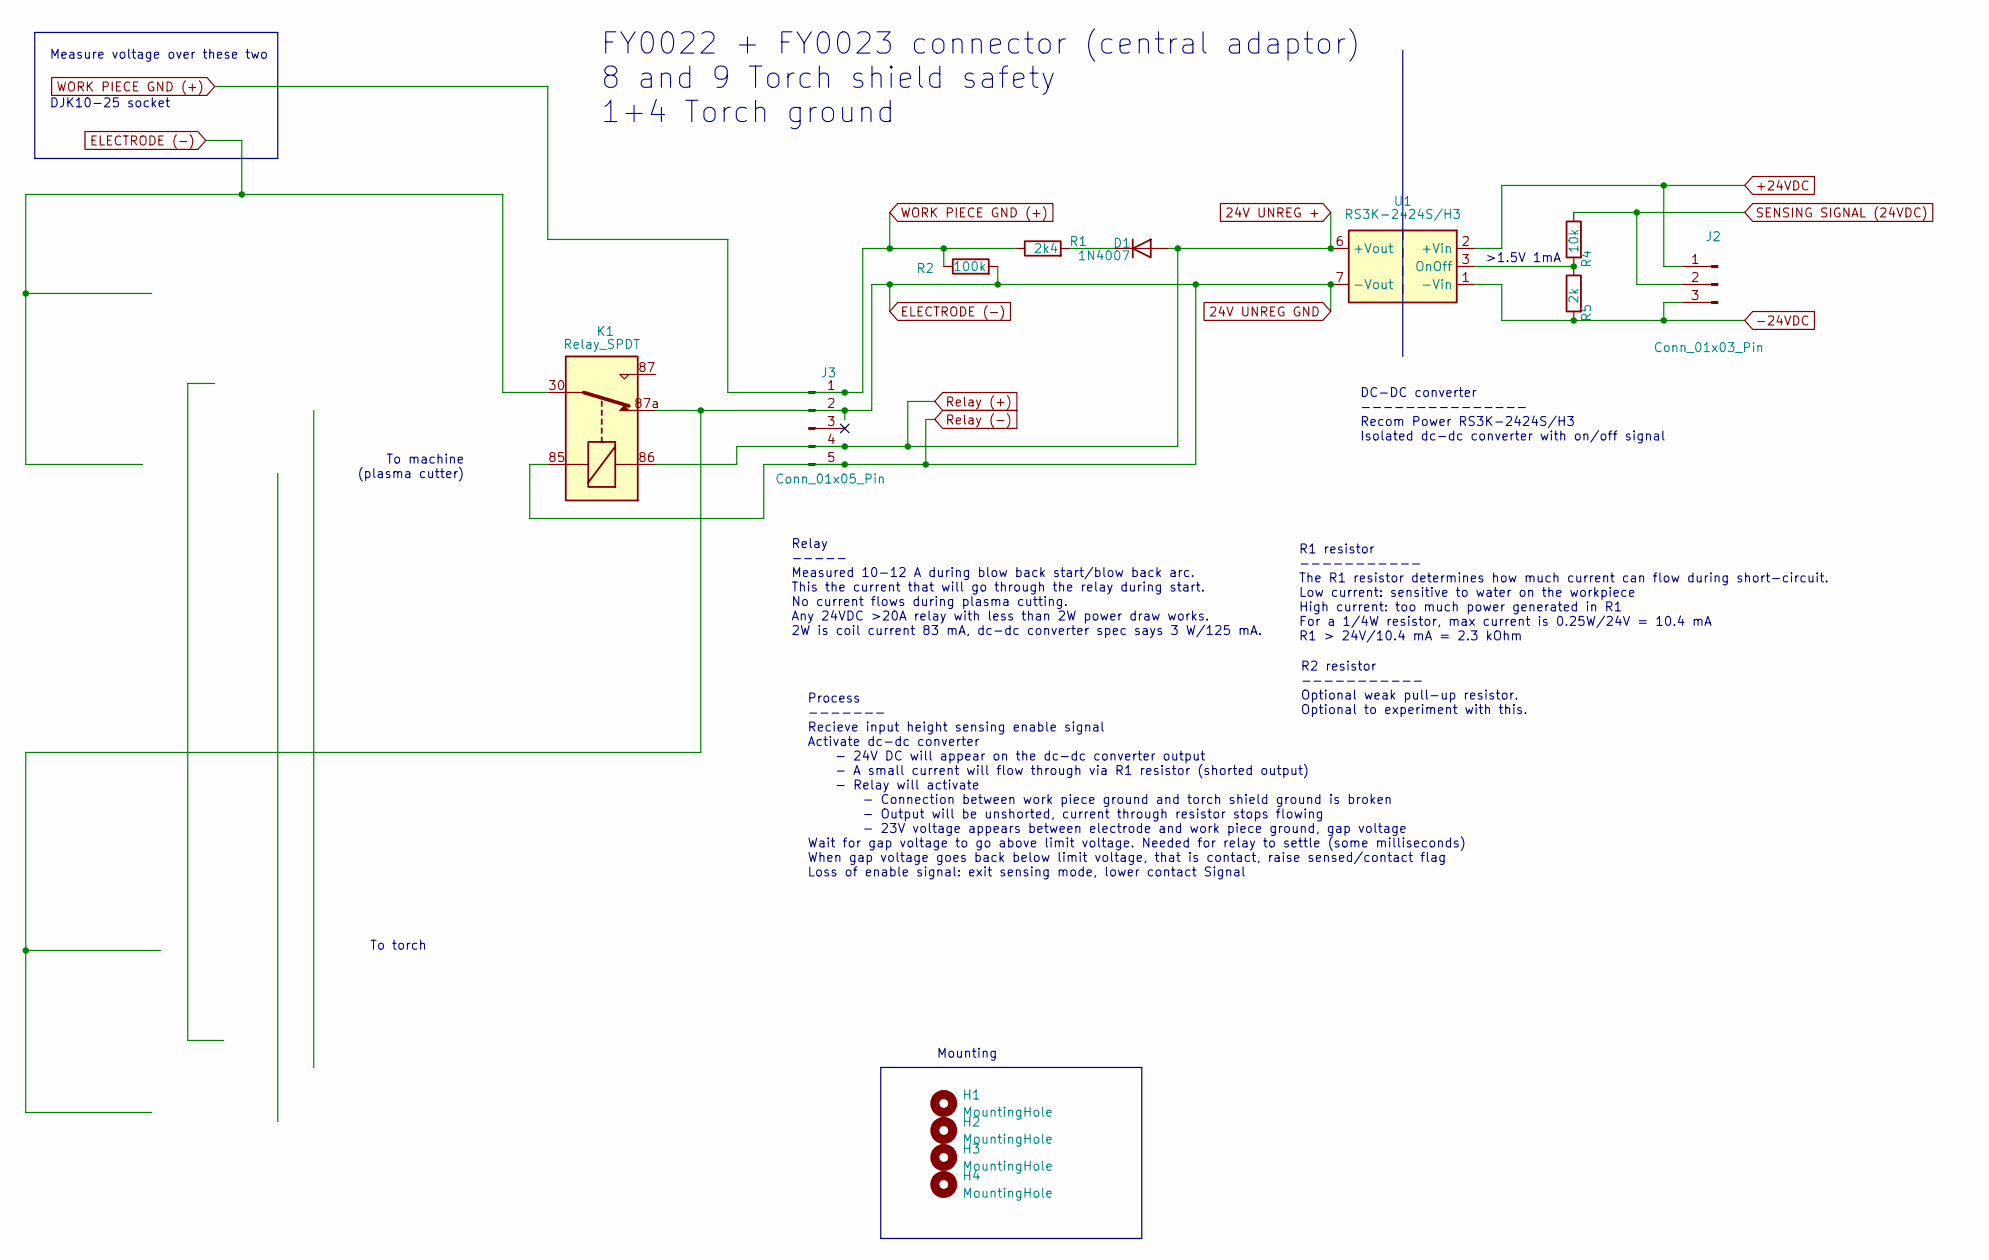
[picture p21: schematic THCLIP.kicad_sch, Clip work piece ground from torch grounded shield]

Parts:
D1: 1N4007; D_DO-41_SOD81_P10.16mm_Horizontal
H1, H2, H3, H4: MountingHole; MountingHole_3.2mm_M3
J2: Conn_01x03_Pin; PhoenixContact_MCV_1,5_3-G-3.5_1x03_P3.50mm_Vertical
J3: Conn_01x05_Pin; PhoenixContact_MCV_1,5_5-G-3.5_1x05_P3.50mm_Vertical
K1: Relay_SPDT
R1: 2k4; R_Axial_DIN0207_L6.3mm_D2.5mm_P10.16mm_Horizontal
R2: 100k; R_Axial_DIN0207_L6.3mm_D2.5mm_P10.16mm_Horizontal
R4: 10k; R_0805_2012Metric_Pad1.20x1.40mm_HandSolder
R5: 2k; R_0805_2012Metric_Pad1.20x1.40mm_HandSolder
U1: RS3K-2424S/H3; Converter_DCDC_TRACO_TEC3-24xxUI_THT

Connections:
24V UNREG +: D1.2 (A), J3.4, K1.86, U1.6 (+Vout)
24V UNREG GND: J3.2, J3.5, K1.30, K1.85, K1.87a, R2.2, U1.7 (-Vout)
+24VDC: J2.1, U1.2 (+Vin)
-24VDC: J2.3, R5.2, U1.1 (-Vin)
unnamed: D1.1 (K), R1.2
unnamed: R4.2, R5.1, U1.3 (OnOff)
SENSING SIGNAL (24VDC): J2.2, R4.1
WORK PIECE GND (+): J3.1, R1.1, R2.1

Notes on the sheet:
DJK10-25 socket
Process ------- Recieve input height sensing enable signal Activate dc-dc converter - 24V DC will appear on the dc-dc converter output - A small current will flow through via R1 resistor (shorted output) - Relay will activate - Connection between work piece ground and torch shield ground is broken 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
>1.5V 1mA
To torch
Mounting
To machine (plasma cutter)
FY0022 + FY0023 connector (central adaptor) 8 and 9 Torch shield safety 1+4 Torch ground
Measure voltage over these two
R1 resistor ----------- The R1 resistor determines how much current can flow during short-circuit. Low current: sensitive to water on the workpiece High current: too much power generated in R1 For a 1/4W resistor, max current is 0.25W/24V = 10.4 mA R1 > 24V/10.4 mA = 2.3 kOhm
DC-DC converter --------------- Recom Power RS3K-2424S/H3 Isolated dc-dc converter with on/off signal
R2 resistor ----------- Optional weak pull-up resistor. Optional to experiment with this.
Relay ----- Measured 10-12 A during blow back start/blow back arc. This the current that will go through the relay during start. No current flows during plasma cutting. Any 24VDC >20A relay with less than 2W power draw works. 2W is coil current 83 mA, dc-dc converter spec says 3 W/125 mA.

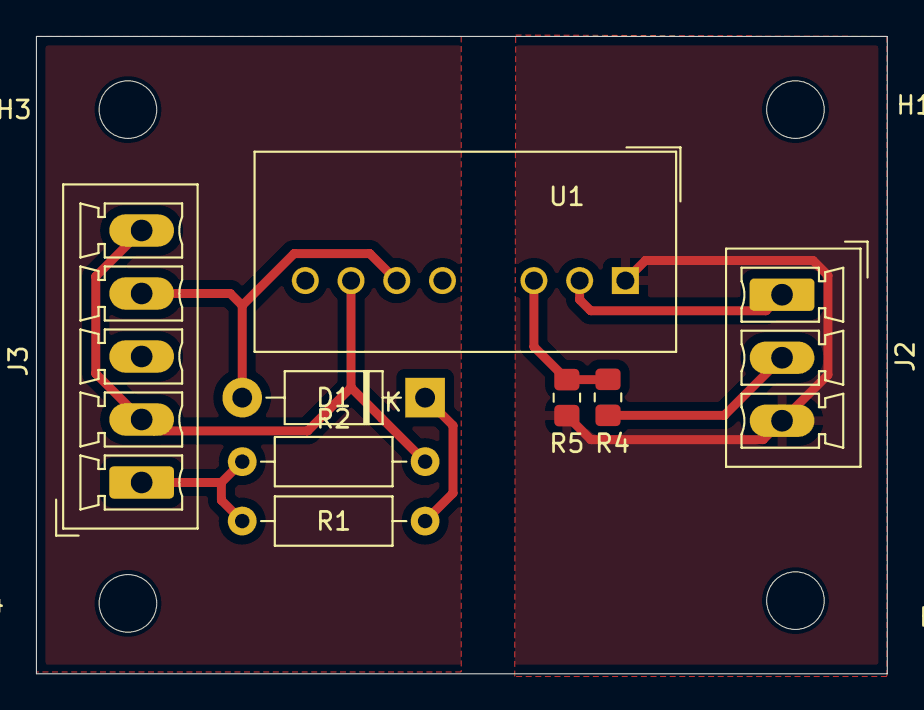
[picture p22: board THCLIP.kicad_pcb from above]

Board: 2 copper layers, 47.3 x 35.4 mm, 12 parts (0 on the bottom side), 8 nets.

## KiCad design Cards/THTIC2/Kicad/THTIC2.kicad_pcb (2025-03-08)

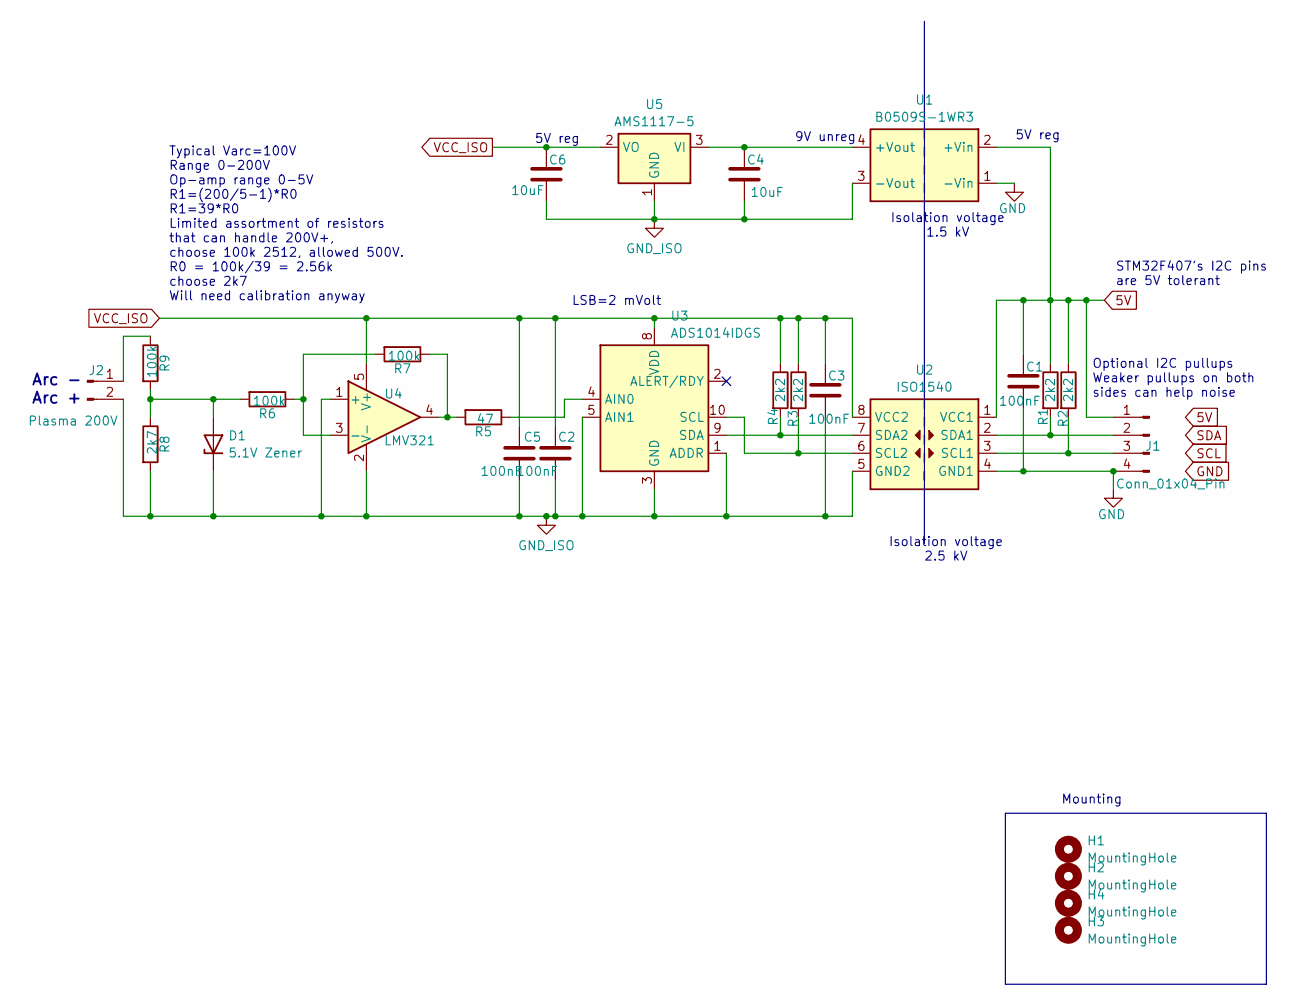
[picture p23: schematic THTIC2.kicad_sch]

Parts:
C1, C2, C3, C5: 100nF; C_0805_2012Metric
C4, C6: 10uF; C_0805_2012Metric
D1: 5.1V Zener; D_SOD-323_HandSoldering
H1, H2, H3, H4: MountingHole; MountingHole_3.2mm_M3
J1: Conn_01x04_Pin; PhoenixContact_MCV_1,5_4-G-3.5_1x04_P3.50mm_Vertical
J2: Plasma 200V; PhoenixContact_MCV_1,5_2-G-3.5_1x02_P3.50mm_Vertical
R1, R2, R3, R4: 2k2; R_0805_2012Metric
R5: 47; R_0805_2012Metric
R6, R7: 100k; R_0805_2012Metric
R8: 2k7; R_0805_2012Metric
R9: 100k; R_2512_6332Metric
U1: B0509S-1WR3; Converter_DCDC_TRACO_TEA1-xxxx_THT
U2: ISO1540; SOIC-8_3.9x4.9mm_P1.27mm
U3: ADS1014IDGS; TSSOP-10_3x3mm_P0.5mm
U4: LMV321; SOT-23-5
U5: AMS1117-5; SOT-223-3_TabPin2

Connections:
5V: C1.1, J1.1, R1.1, R2.1, U1.2 (+Vin), U2.1 (VCC1)
GND: C1.2, J1.4, U1.1 (-Vin), U2.4 (GND1)
GND_ISO: C2.2, C3.2, C4.2, C5.2, C6.2, D1.1 (K), J2.2, R8.2, U1.3 (-Vout), U2.5 (GND2), U3.1 (ADDR), U3.3 (GND), U3.5 (AIN1), U4.1 (+), U4.2 (V-), U5.1 (GND)
unnamed: D1.2 (A), R6.2, R8.1, R9.2
unnamed: J1.2, R1.2, U2.2 (SDA1)
unnamed: J1.3, R2.2, U2.3 (SCL1)
unnamed: J2.1, R9.1
unnamed: R5.2, R7.1, U4.4
unnamed: C4.1, U1.4 (+Vout), U5.3 (VI)
unnamed: R3.2, U2.6 (SCL2), U3.10 (SCL)
unnamed: R4.2, U2.7 (SDA2), U3.9 (SDA)
unnamed: R5.1, U3.4 (AIN0)
unnamed: R6.1, R7.2, U4.3 (-)
VCC_ISO: C2.1, C3.1, C5.1, C6.1, R3.1, R4.1, U2.8 (VCC2), U3.8 (VDD), U4.5 (V+), U5.2 (VO)

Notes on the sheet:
Mounting
5V reg
Isolation voltage 2.5 kV
STM32F407's I2C pins are 5V tolerant
9V unreg
LSB=2 mVolt
Optional I2C pullups Weaker pullups on both sides can help noise
Isolation voltage 1.5 kV
Typical Varc=100V Range 0-200V Op-amp range 0-5V R1=(200/5-1)*R0 R1=39*R0 Limited assortment of resistors that can handle 200V+, choose 100k 2512, allowed 500V. R0 = 100k/39 = 2.56k choose 2k7 Will need calibration anyway
Arc - Arc +

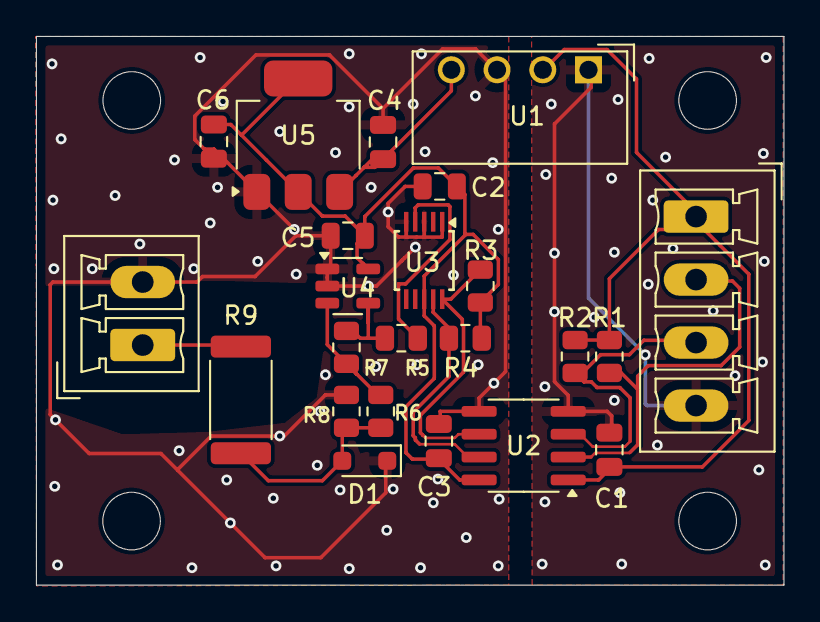
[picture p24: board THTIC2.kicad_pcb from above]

Board: 2 copper layers, 41.5 x 30.5 mm, 27 parts (0 on the bottom side), 14 nets.

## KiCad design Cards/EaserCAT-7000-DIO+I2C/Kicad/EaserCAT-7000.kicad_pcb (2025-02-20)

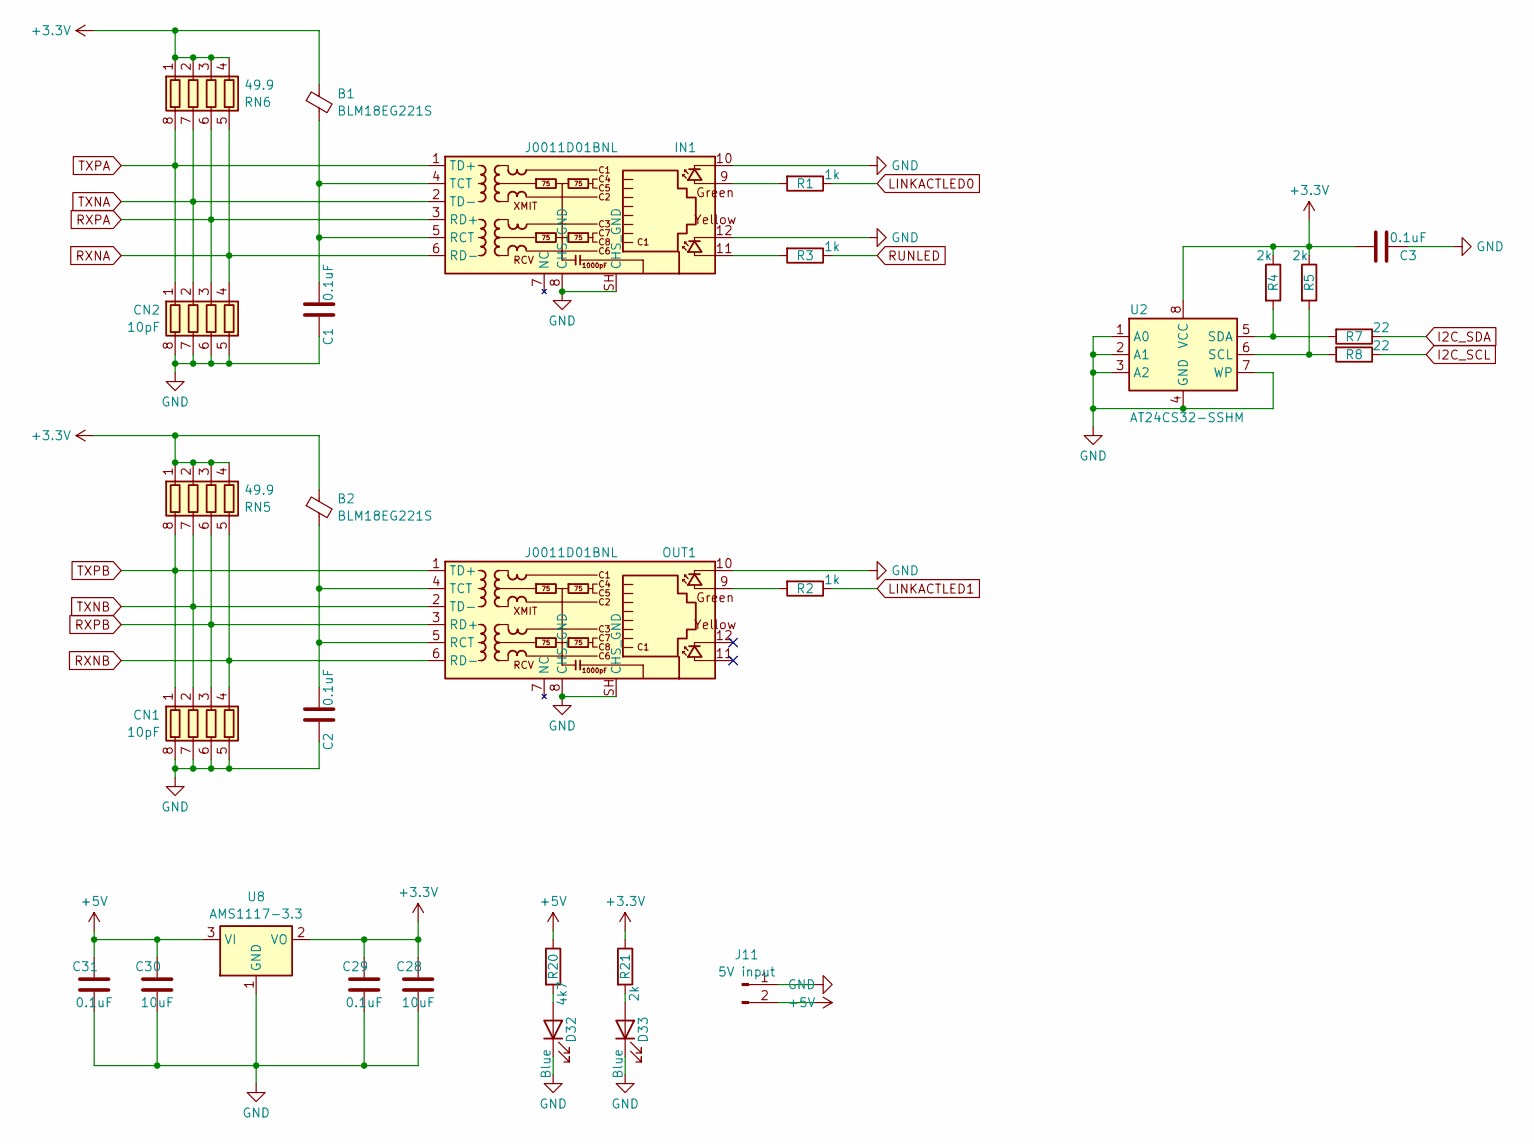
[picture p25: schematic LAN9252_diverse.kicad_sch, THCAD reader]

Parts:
B1, B2: BLM18EG221S; C_0805_2012Metric
C1, C2, C3, C29, C31: 0.1uF; C_0603_1608Metric
C28, C30: 10uF; C_0603_1608Metric
CN1, CN2: 10pF; R_Array_Convex_4x0603
D32, D33: Blue; LED_0603_1608Metric
IN1: J0011D01BNL; PulseJack JB0011D01BNL
J11: 5V input; PhoenixContact_MCV_1,5_2-G-3.5_1x02_P3.50mm_Vertical
OUT1: J0011D01BNL; PulseJack JB0011D01BNL
R1, R2, R3: 1k; R_0603_1608Metric
R4, R5, R21: 2k; R_0603_1608Metric
R7, R8: 22; R_0603_1608Metric
R20: 4k7; R_0603_1608Metric
RN5, RN6: 49.9; R_Array_Convex_4x0603
U2: AT24CS32-SSHM; SOIC-8_3.9x4.9mm_P1.27mm
U8: AMS1117-3.3; SOT-223-3_TabPin2

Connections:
+3.3V: B1.1, B2.1, C3.2, C28.1, C29.1, R4.1, R5.1, R21.1, RN5.1 (R1.1), RN5.2 (R2.1), RN5.3 (R3.1), RN5.4 (R4.1), RN6.1 (R1.1), RN6.2 (R2.1), RN6.3 (R3.1), RN6.4 (R4.1), U2.8 (VCC), U8.2 (VO); also elsewhere on the board
+5V: C30.1, C31.1, J11.2, R20.1, U8.3 (VI); also elsewhere on the board
GND: C1.1, C2.1, C3.1, C28.2, C29.2, C30.2, C31.2, CN1.5 (R4.2), CN1.6 (R3.2), CN1.7 (R2.2), CN1.8 (R1.2), CN2.5 (R4.2), CN2.6 (R3.2), CN2.7 (R2.2), CN2.8 (R1.2), D32.1 (K), D33.1 (K), IN1.8 (CHS_GND), IN1.10, IN1.12, IN1.SH (CHS_GND), J11.1, OUT1.8 (CHS_GND), OUT1.10, OUT1.SH (CHS_GND), U2.1 (A0), U2.2 (A1), U2.3 (A2), U2.4 (GND), U2.7 (WP), U8.1 (GND); also elsewhere on the board
I2C_SCL: R8.1; also elsewhere on the board
I2C_SDA: R7.1; also elsewhere on the board
LINKACTLED0: R1.1; also elsewhere on the board
LINKACTLED1: R2.1; also elsewhere on the board
unnamed: D32.2 (A), R20.2
unnamed: D33.2 (A), R21.2
unnamed: IN1.9, R1.2
unnamed: IN1.11, R3.2
unnamed: B1.2, C1.2, IN1.4 (TCT), IN1.5 (RCT)
unnamed: OUT1.9, R2.2
unnamed: B2.2, C2.2, OUT1.4 (TCT), OUT1.5 (RCT)
unnamed: R5.2, R8.2, U2.6 (SCL)
unnamed: R4.2, R7.2, U2.5 (SDA)
RUNLED: R3.1; also elsewhere on the board
RXNA: CN2.4 (R4.1), IN1.6 (RD-), RN6.5 (R4.2); also elsewhere on the board
RXNB: CN1.4 (R4.1), OUT1.6 (RD-), RN5.5 (R4.2); also elsewhere on the board
RXPA: CN2.3 (R3.1), IN1.3 (RD+), RN6.6 (R3.2); also elsewhere on the board
RXPB: CN1.3 (R3.1), OUT1.3 (RD+), RN5.6 (R3.2); also elsewhere on the board
TXNA: CN2.2 (R2.1), IN1.2 (TD-), RN6.7 (R2.2); also elsewhere on the board
TXNB: CN1.2 (R2.1), OUT1.2 (TD-), RN5.7 (R2.2); also elsewhere on the board
TXPA: CN2.1 (R1.1), IN1.1 (TD+), RN6.8 (R1.2); also elsewhere on the board
TXPB: CN1.1 (R1.1), OUT1.1 (TD+), RN5.8 (R1.2); also elsewhere on the board

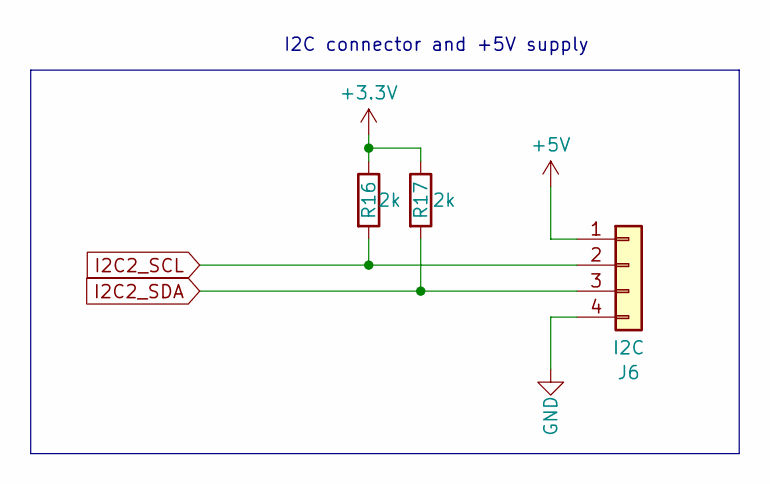
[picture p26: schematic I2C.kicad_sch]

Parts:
J6: I2C; PhoenixContact_MCV_1,5_4-G-3.5_1x04_P3.50mm_Vertical
R16, R17: 2k; R_0603_1608Metric

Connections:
+3.3V: R16.1, R17.1; also elsewhere on the board
+5V: J6.1; also elsewhere on the board
GND: J6.4; also elsewhere on the board
I2C2_SCL: J6.2, R16.2; also elsewhere on the board
I2C2_SDA: J6.3, R17.2; also elsewhere on the board

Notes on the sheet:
I2C connector and +5V supply

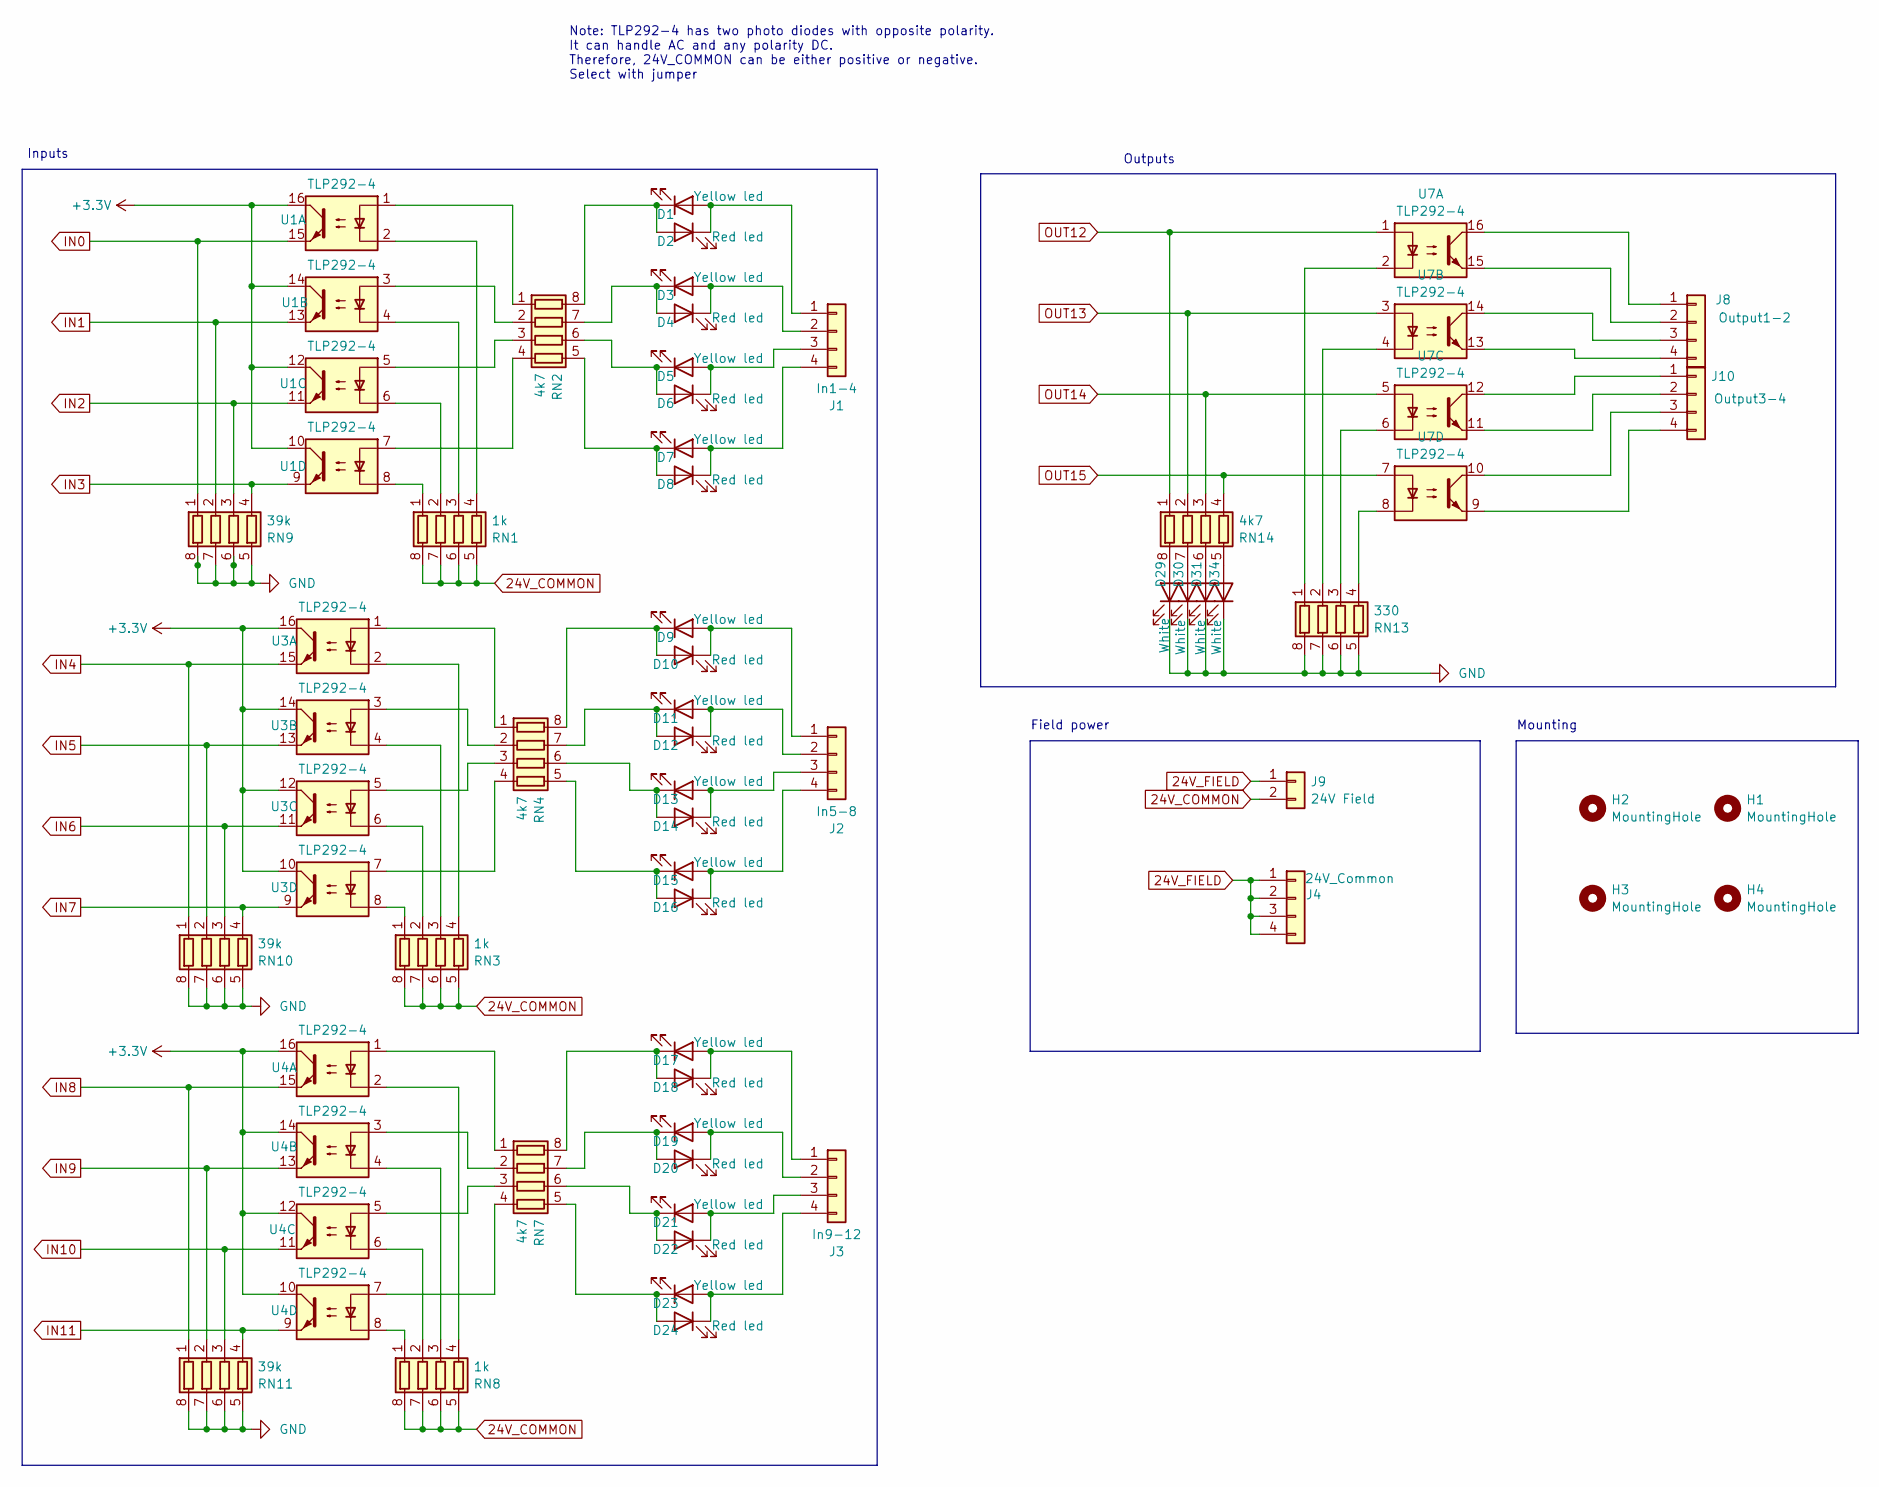
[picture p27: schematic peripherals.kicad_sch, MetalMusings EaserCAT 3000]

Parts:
D1, D3, D5, D7, D9, D11, D13, D15, D17, D19, D21, D23: Yellow led; LED_0603_1608Metric
D2, D4, D6, D8, D10, D12, D14, D16, D18, D20, D22, D24: Red led; LED_0603_1608Metric
D29, D30, D31, D34: White; LED_0603_1608Metric
H1, H2, H3, H4: MountingHole; MountingHole_3.2mm_M3_ISO14580
J1: In1-4; PhoenixContact_MCV_1,5_4-G-3.5_1x04_P3.50mm_Vertical
J2: In5-8; PhoenixContact_MCV_1,5_4-G-3.5_1x04_P3.50mm_Vertical
J3: In9-12; PhoenixContact_MCV_1,5_4-G-3.5_1x04_P3.50mm_Vertical
J4: 24V_Common; PhoenixContact_MCV_1,5_4-G-3.5_1x04_P3.50mm_Vertical
J8: Output1-2; PhoenixContact_MCV_1,5_4-G-3.5_1x04_P3.50mm_Vertical
J9: 24V Field; PhoenixContact_MCV_1,5_2-G-3.5_1x02_P3.50mm_Vertical
J10: Output3-4; PhoenixContact_MCV_1,5_4-G-3.5_1x04_P3.50mm_Vertical
RN1, RN3, RN8: 1k; R_Array_Convex_4x0603
RN2, RN4, RN7, RN14: 4k7; R_Array_Convex_4x0603
RN9, RN10, RN11: 39k; R_Array_Convex_4x0603
RN13: 330; R_Array_Convex_4x0603
U1, U3, U4, U7: TLP292-4; SOIC-16_4.55x10.3mm_P1.27mm

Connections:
24V_COMMON: J9.2, RN1.5 (R4.2), RN1.6 (R3.2), RN1.7 (R2.2), RN1.8 (R1.2), RN3.5 (R4.2), RN3.6 (R3.2), RN3.7 (R2.2), RN3.8 (R1.2), RN8.5 (R4.2), RN8.6 (R3.2), RN8.7 (R2.2), RN8.8 (R1.2)
24V_FIELD: J4.1, J4.2, J4.3, J4.4, J9.1
+3.3V: U1.10, U1.12, U1.14, U1.16, U3.10, U3.12, U3.14, U3.16, U4.10, U4.12, U4.14, U4.16; also elsewhere on the board
GND: D29.1 (K), D30.1 (K), D31.1 (K), D34.1 (K), RN9.5 (R4.2), RN9.6 (R3.2), RN9.7 (R2.2), RN9.8 (R1.2), RN10.5 (R4.2), RN10.6 (R3.2), RN10.7 (R2.2), RN10.8 (R1.2), RN11.5 (R4.2), RN11.6 (R3.2), RN11.7 (R2.2), RN11.8 (R1.2), RN13.5 (R4.2), RN13.6 (R3.2), RN13.7 (R2.2), RN13.8 (R1.2); also elsewhere on the board
IN0: RN9.1 (R1.1), U1.15; also elsewhere on the board
IN1: RN9.2 (R2.1), U1.13; also elsewhere on the board
IN2: RN9.3 (R3.1), U1.11; also elsewhere on the board
IN3: RN9.4 (R4.1), U1.9; also elsewhere on the board
IN4: RN10.1 (R1.1), U3.15; also elsewhere on the board
IN5: RN10.2 (R2.1), U3.13; also elsewhere on the board
IN6: RN10.3 (R3.1), U3.11; also elsewhere on the board
IN7: RN10.4 (R4.1), U3.9; also elsewhere on the board
IN8: RN11.1 (R1.1), U4.15; also elsewhere on the board
IN9: RN11.2 (R2.1), U4.13; also elsewhere on the board
IN10: RN11.3 (R3.1), U4.11; also elsewhere on the board
IN11: RN11.4 (R4.1), U4.9; also elsewhere on the board
unnamed: D1.2 (A), D2.1 (K), J1.1
unnamed: D1.1 (K), D2.2 (A), RN2.8 (R1.2)
unnamed: D3.2 (A), D4.1 (K), J1.2
unnamed: D3.1 (K), D4.2 (A), RN2.7 (R2.2)
unnamed: D5.2 (A), D6.1 (K), J1.3
unnamed: D5.1 (K), D6.2 (A), RN2.6 (R3.2)
unnamed: D7.2 (A), D8.1 (K), J1.4
unnamed: D7.1 (K), D8.2 (A), RN2.5 (R4.2)
unnamed: D9.1 (K), D10.2 (A), RN4.8 (R1.2)
unnamed: D9.2 (A), D10.1 (K), J2.1
unnamed: D11.2 (A), D12.1 (K), J2.2
unnamed: D11.1 (K), D12.2 (A), RN4.7 (R2.2)
unnamed: D13.2 (A), D14.1 (K), J2.3
unnamed: D13.1 (K), D14.2 (A), RN4.6 (R3.2)
unnamed: D15.2 (A), D16.1 (K), J2.4
unnamed: D15.1 (K), D16.2 (A), RN4.5 (R4.2)
unnamed: D17.2 (A), D18.1 (K), J3.1
unnamed: D17.1 (K), D18.2 (A), RN7.8 (R1.2)
unnamed: D19.2 (A), D20.1 (K), J3.2
unnamed: D19.1 (K), D20.2 (A), RN7.7 (R2.2)
unnamed: D21.2 (A), D22.1 (K), J3.3
unnamed: D21.1 (K), D22.2 (A), RN7.6 (R3.2)
unnamed: D23.2 (A), D24.1 (K), J3.4
unnamed: D23.1 (K), D24.2 (A), RN7.5 (R4.2)
unnamed: D34.2 (A), RN14.5 (R4.2)
unnamed: D31.2 (A), RN14.6 (R3.2)
unnamed: D30.2 (A), RN14.7 (R2.2)
unnamed: D29.2 (A), RN14.8 (R1.2)
unnamed: J8.1, U7.16
unnamed: J8.2, U7.15
unnamed: J8.3, U7.14
unnamed: J8.4, U7.13
unnamed: J10.1, U7.12
unnamed: J10.2, U7.11
unnamed: J10.3, U7.10
unnamed: J10.4, U7.9
unnamed: RN1.1 (R1.1), U1.8
unnamed: RN1.2 (R2.1), U1.6
unnamed: RN1.3 (R3.1), U1.4
unnamed: RN1.4 (R4.1), U1.2
unnamed: RN2.1 (R1.1), U1.1
unnamed: RN2.2 (R2.1), U1.3
unnamed: RN2.3 (R3.1), U1.5
unnamed: RN2.4 (R4.1), U1.7
unnamed: RN3.1 (R1.1), U3.8
unnamed: RN3.2 (R2.1), U3.6
unnamed: RN3.3 (R3.1), U3.4
unnamed: RN3.4 (R4.1), U3.2
unnamed: RN4.1 (R1.1), U3.1
unnamed: RN4.2 (R2.1), U3.3
unnamed: RN4.3 (R3.1), U3.5
unnamed: RN4.4 (R4.1), U3.7
unnamed: RN7.1 (R1.1), U4.1
unnamed: RN7.2 (R2.1), U4.3
unnamed: RN7.3 (R3.1), U4.5
unnamed: RN7.4 (R4.1), U4.7
unnamed: RN8.1 (R1.1), U4.8
unnamed: RN8.2 (R2.1), U4.6
unnamed: RN8.3 (R3.1), U4.4
unnamed: RN8.4 (R4.1), U4.2
unnamed: RN13.1 (R1.1), U7.2
unnamed: RN13.2 (R2.1), U7.4
unnamed: RN13.3 (R3.1), U7.6
unnamed: RN13.4 (R4.1), U7.8
OUT12: RN14.1 (R1.1), U7.1; also elsewhere on the board
OUT13: RN14.2 (R2.1), U7.3; also elsewhere on the board
OUT14: RN14.3 (R3.1), U7.5; also elsewhere on the board
OUT15: RN14.4 (R4.1), U7.7; also elsewhere on the board

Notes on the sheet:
Inputs
Mounting
Outputs
Field power
Note: TLP292-4 has two photo diodes with opposite polarity. It can handle AC and any polarity DC. Therefore, 24V_COMMON can be either positive or negative. Select with jumper

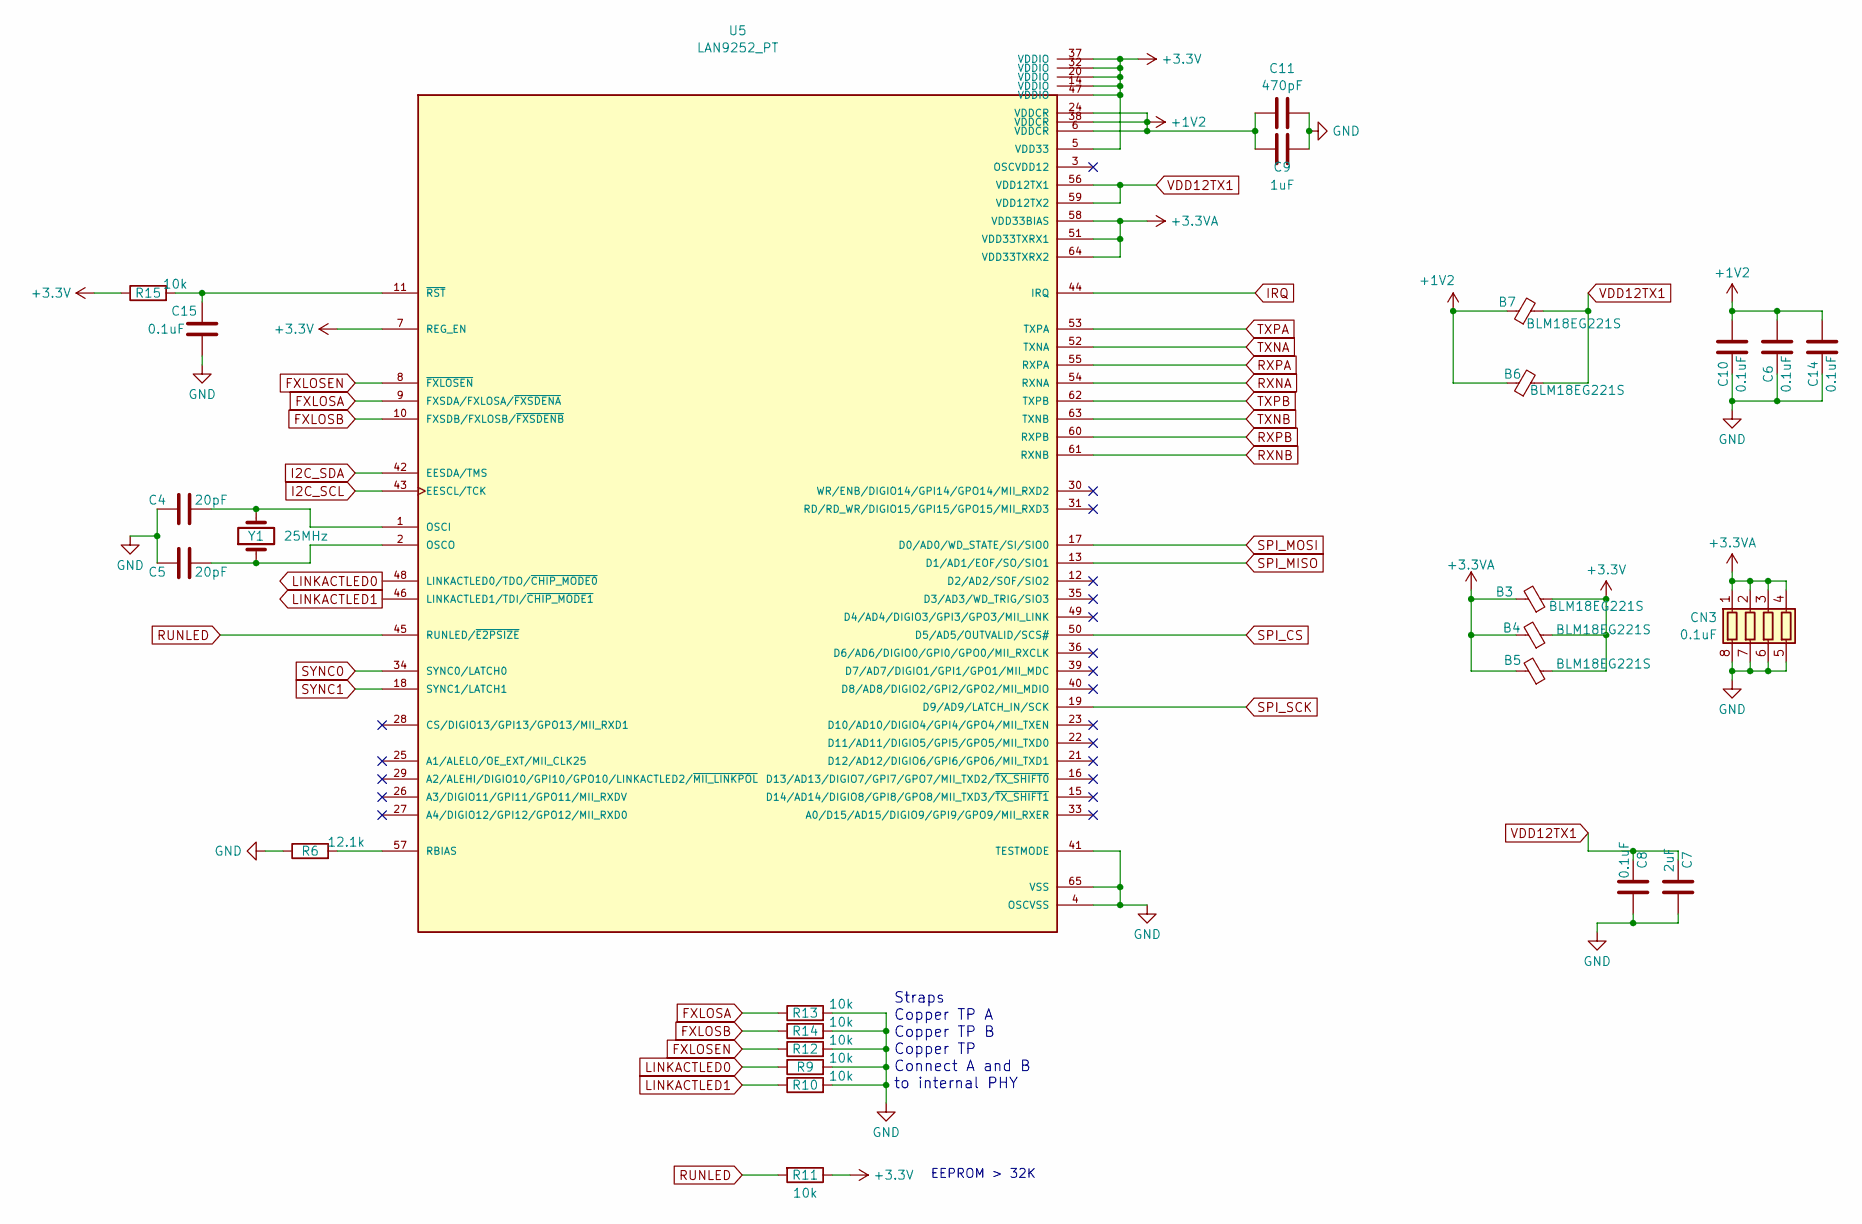
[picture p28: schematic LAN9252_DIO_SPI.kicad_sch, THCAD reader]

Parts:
B3, B4, B5, B6, B7: BLM18EG221S; C_0805_2012Metric
C4, C5: 20pF; C_0603_1608Metric
C6, C8, C10, C14, C15: 0.1uF; C_0603_1608Metric
C7: 2uF; C_0603_1608Metric
C9: 1uF; C_0603_1608Metric
C11: 470pF; C_0603_1608Metric
CN3: 0.1uF; R_Array_Convex_4x0603
R6: 12.1k; R_0603_1608Metric
R9, R10, R11, R12, R13, R14, R15: 10k; R_0603_1608Metric
U5: LAN9252_PT; TQFP-64-1EP_10x10mm_P0.5mm_EP8x8mm; PARTREV 04-08-15
Y1: 25MHz; Crystal_HC49-4H_Vertical

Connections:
+1V2: B6.1, B7.1, C6.2, C9.1, C10.2, C11.1, C14.2, U5.6 (VDDCR), U5.24 (VDDCR), U5.38 (VDDCR)
+3.3V: B3.1, B4.1, B5.1, R11.1, R15.1, U5.5 (VDD33), U5.7 (REG_EN), U5.14 (VDDIO), U5.20 (VDDIO), U5.32 (VDDIO), U5.37 (VDDIO), U5.47 (VDDIO); also elsewhere on the board
+3.3VA: B3.2, B4.2, B5.2, CN3.1 (R1.1), CN3.2 (R2.1), CN3.3 (R3.1), CN3.4 (R4.1), U5.51 (VDD33TXRX1), U5.58 (VDD33BIAS), U5.64 (VDD33TXRX2)
FXLOSA: R13.1, U5.9 (FXSDA/FXLOSA/~FXSDENA)
FXLOSB: R14.1, U5.10 (FXSDB/FXLOSB/~FXSDENB)
FXLOSEN: R12.1, U5.8 (~FXLOSEN)
GND: C4.1, C5.1, C6.1, C7.2, C8.2, C9.2, C10.1, C11.2, C14.1, C15.1, CN3.5 (R4.2), CN3.6 (R3.2), CN3.7 (R2.2), CN3.8 (R1.2), R6.1, R9.2, R10.2, R12.2, R13.2, R14.2, U5.4 (OSCVSS), U5.41 (TESTMODE), U5.65 (VSS); also elsewhere on the board
I2C_SCL: U5.43 (EESCL/TCK); also elsewhere on the board
I2C_SDA: U5.42 (EESDA/TMS); also elsewhere on the board
IRQ: U5.44 (IRQ); also elsewhere on the board
LINKACTLED0: R9.1, U5.48 (LINKACTLED0/TDO/~CHIP_MODE0); also elsewhere on the board
LINKACTLED1: R10.1, U5.46 (LINKACTLED1/TDI/~CHIP_MODE1); also elsewhere on the board
unnamed: C4.2, U5.1 (OSCI), Y1.2
unnamed: C5.2, U5.2 (OSCO), Y1.1
unnamed: R6.2, U5.57 (RBIAS)
unnamed: C15.2, R15.2, U5.11 (~RST)
RUNLED: R11.2, U5.45 (RUNLED/~E2PSIZE); also elsewhere on the board
RXNA: U5.54 (RXNA); also elsewhere on the board
RXNB: U5.61 (RXNB); also elsewhere on the board
RXPA: U5.55 (RXPA); also elsewhere on the board
RXPB: U5.60 (RXPB); also elsewhere on the board
SPI_CS: U5.50 (D5/AD5/OUTVALID/SCS#); also elsewhere on the board
SPI_MISO: U5.13 (D1/AD1/EOF/SO/SIO1); also elsewhere on the board
SPI_MOSI: U5.17 (D0/AD0/WD_STATE/SI/SIO0); also elsewhere on the board
SPI_SCK: U5.19 (D9/AD9/LATCH_IN/SCK); also elsewhere on the board
SYNC0: U5.34 (SYNC0/LATCH0); also elsewhere on the board
SYNC1: U5.18 (SYNC1/LATCH1); also elsewhere on the board
TXNA: U5.52 (TXNA); also elsewhere on the board
TXNB: U5.63 (TXNB); also elsewhere on the board
TXPA: U5.53 (TXPA); also elsewhere on the board
TXPB: U5.62 (TXPB); also elsewhere on the board
VDD12TX1: B6.2, B7.2, C7.1, C8.1, U5.56 (VDD12TX1), U5.59 (VDD12TX2)

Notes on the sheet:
Straps Copper TP A Copper TP B Copper TP Connect A and B to internal PHY
EEPROM > 32K

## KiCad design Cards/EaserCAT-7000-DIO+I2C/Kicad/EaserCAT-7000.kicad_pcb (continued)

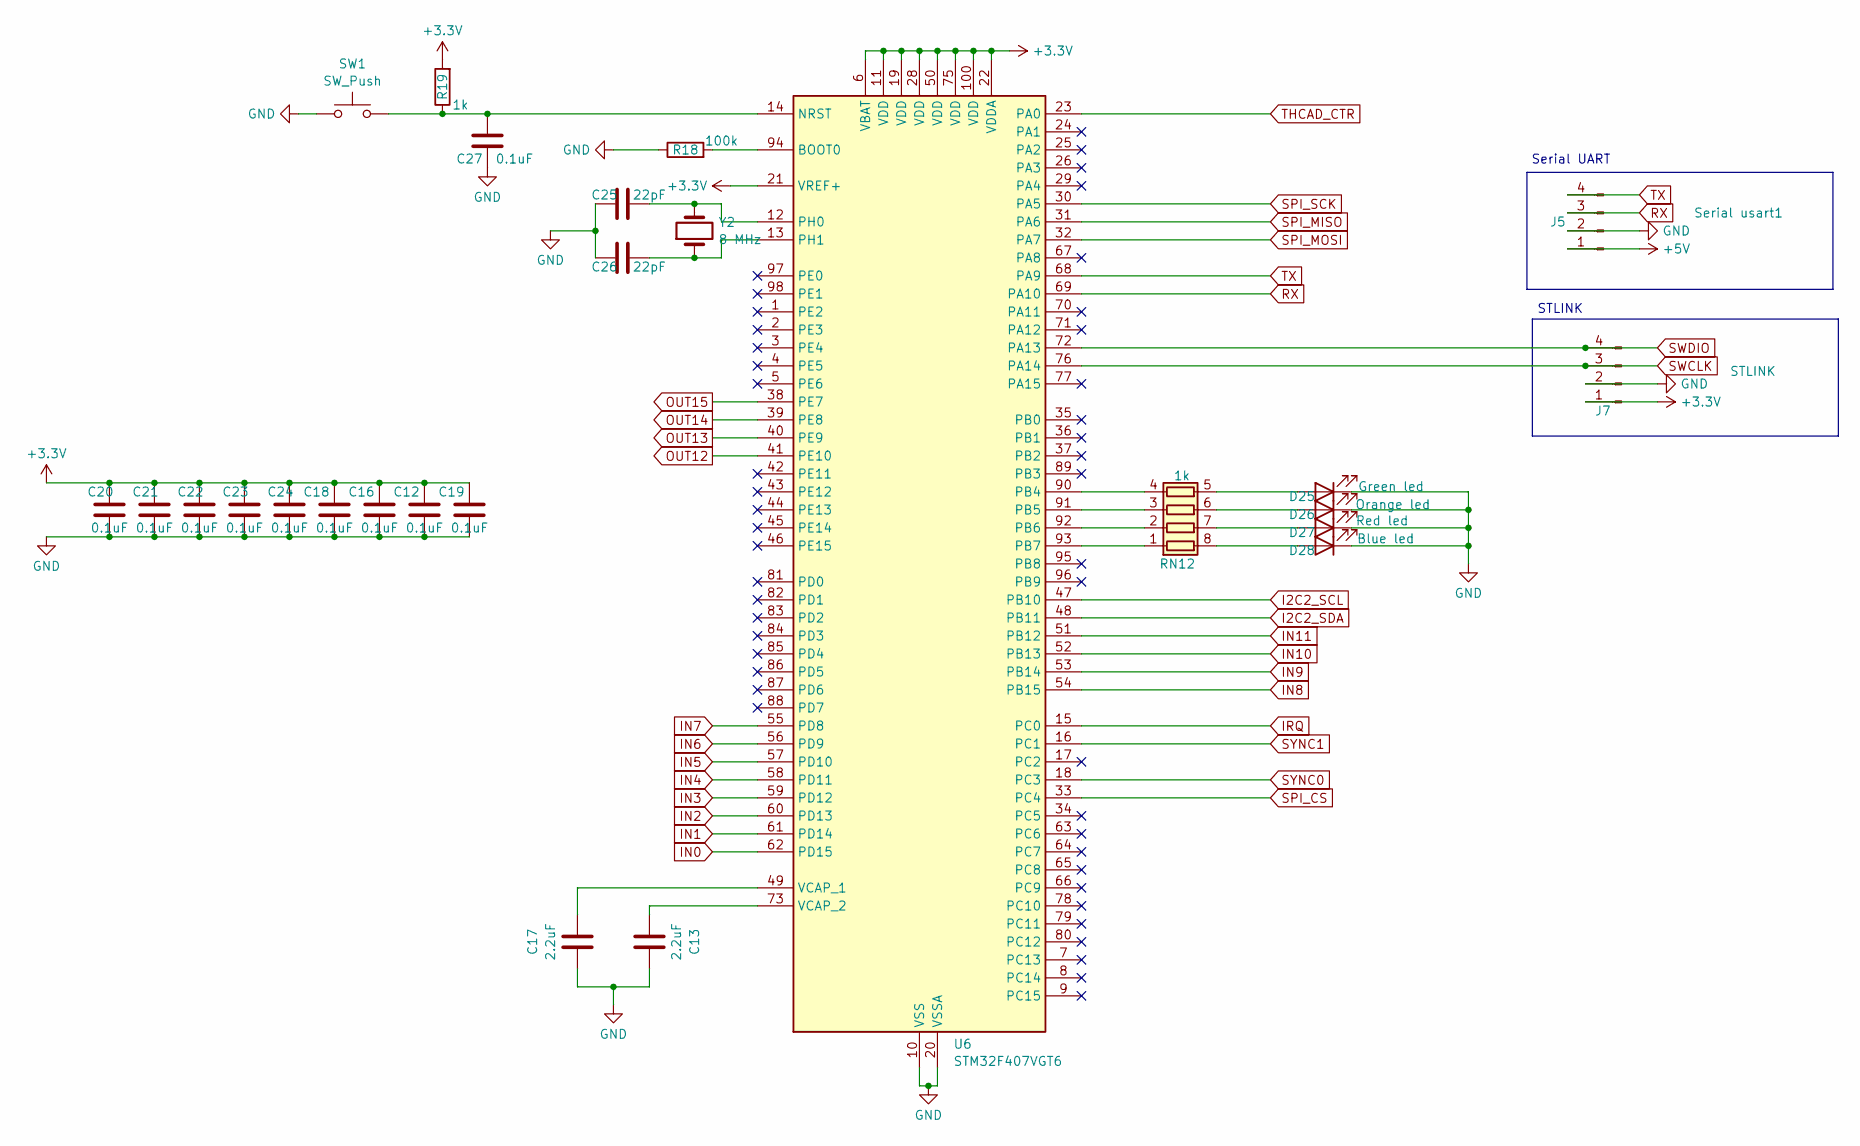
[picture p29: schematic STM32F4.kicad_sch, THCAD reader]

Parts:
C12, C16, C18, C19, C20, C21, C22, C23, C24, C27: 0.1uF; C_0603_1608Metric
C13, C17: 2.2uF; C_0603_1608Metric
C25, C26: 22pF; C_0603_1608Metric
D25: Green led; LED_0603_1608Metric
D26: Orange led; LED_0603_1608Metric
D27: Red led; LED_0603_1608Metric
D28: Blue led; LED_0603_1608Metric
J5: Serial usart1; JST_XH_B4B-XH-A_1x04_P2.50mm_Vertical
J7: STLINK; JST_XH_B4B-XH-A_1x04_P2.50mm_Vertical
R18: 100k; R_0603_1608Metric
R19: 1k; R_0603_1608Metric
RN12: 1k; R_Array_Convex_4x0603
SW1: SW_Push; SW_Push_1P1T_XKB_TS-1187A
U6: STM32F407VGT6; LQFP-100_14x14mm_P0.5mm
Y2: 8 MHz; Crystal_HC49-4H_Vertical

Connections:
+3.3V: C12.1, C16.1, C18.1, C19.1, C20.1, C21.1, C22.1, C23.1, C24.1, J7.1, R19.2, U6.6 (VBAT), U6.11 (VDD), U6.19 (VDD), U6.21 (VREF+), U6.22 (VDDA), U6.28 (VDD), U6.50 (VDD), U6.75 (VDD), U6.100 (VDD); also elsewhere on the board
+5V: J5.1; also elsewhere on the board
GND: C12.2, C13.1, C16.2, C17.1, C18.2, C19.2, C20.2, C21.2, C22.2, C23.2, C24.2, C25.1, C26.1, C27.1, D25.1 (K), D26.1 (K), D27.1 (K), D28.1 (K), J5.2, J7.2, R18.1, SW1.1, U6.10 (VSS), U6.20 (VSSA), U6.27 (VSS), U6.74 (VSS), U6.99 (VSS); also elsewhere on the board
I2C2_SCL: U6.47 (PB10); also elsewhere on the board
I2C2_SDA: U6.48 (PB11); also elsewhere on the board
IN0: U6.62 (PD15); also elsewhere on the board
IN1: U6.61 (PD14); also elsewhere on the board
IN2: U6.60 (PD13); also elsewhere on the board
IN3: U6.59 (PD12); also elsewhere on the board
IN4: U6.58 (PD11); also elsewhere on the board
IN5: U6.57 (PD10); also elsewhere on the board
IN6: U6.56 (PD9); also elsewhere on the board
IN7: U6.55 (PD8); also elsewhere on the board
IN8: U6.54 (PB15); also elsewhere on the board
IN9: U6.53 (PB14); also elsewhere on the board
IN10: U6.52 (PB13); also elsewhere on the board
IN11: U6.51 (PB12); also elsewhere on the board
IRQ: U6.15 (PC0); also elsewhere on the board
unnamed: D25.2 (A), RN12.5 (R4.2)
unnamed: D26.2 (A), RN12.6 (R3.2)
unnamed: D27.2 (A), RN12.7 (R2.2)
unnamed: D28.2 (A), RN12.8 (R1.2)
unnamed: RN12.1 (R1.1), U6.93 (PB7)
unnamed: RN12.2 (R2.1), U6.92 (PB6)
unnamed: RN12.3 (R3.1), U6.91 (PB5)
unnamed: RN12.4 (R4.1), U6.90 (PB4)
unnamed: R18.2, U6.94 (BOOT0)
unnamed: C27.2, R19.1, SW1.2, U6.14 (NRST)
unnamed: C25.2, U6.12 (PH0), Y2.2
unnamed: C26.2, U6.13 (PH1), Y2.1
unnamed: C17.2, U6.49 (VCAP_1)
unnamed: C13.2, U6.73 (VCAP_2)
OUT12: U6.41 (PE10); also elsewhere on the board
OUT13: U6.40 (PE9); also elsewhere on the board
OUT14: U6.39 (PE8); also elsewhere on the board
OUT15: U6.38 (PE7); also elsewhere on the board
RX: J5.3, U6.69 (PA10)
SPI_CS: U6.33 (PC4); also elsewhere on the board
SPI_MISO: U6.31 (PA6); also elsewhere on the board
SPI_MOSI: U6.32 (PA7); also elsewhere on the board
SPI_SCK: U6.30 (PA5); also elsewhere on the board
SWCLK: J7.3, U6.76 (PA14)
SWDIO: J7.4, U6.72 (PA13)
SYNC0: U6.18 (PC3); also elsewhere on the board
SYNC1: U6.16 (PC1); also elsewhere on the board
THCAD_CTR: U6.23 (PA0)
TX: J5.4, U6.68 (PA9)

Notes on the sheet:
STLINK
Serial UART

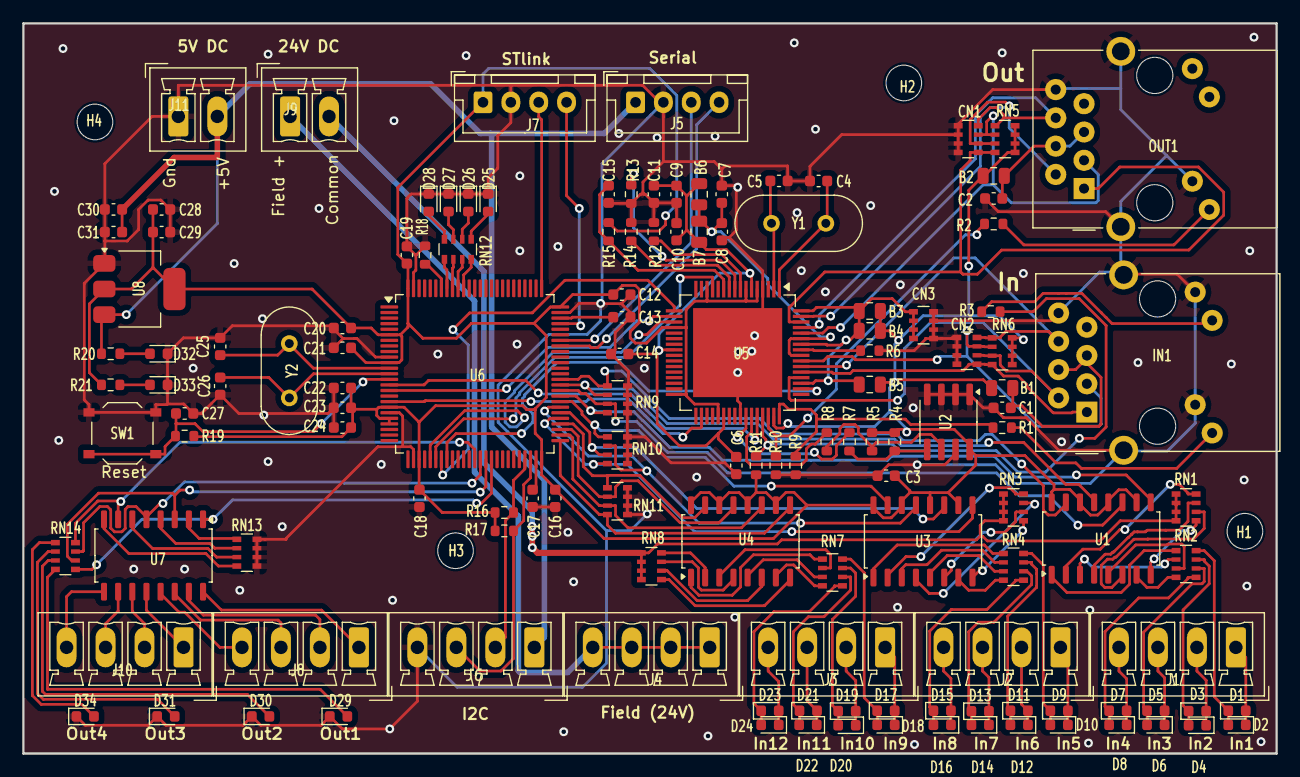
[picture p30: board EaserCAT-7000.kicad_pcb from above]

Board: 2 copper layers, 112.5 x 65.6 mm, 138 parts (0 on the bottom side), 144 nets.

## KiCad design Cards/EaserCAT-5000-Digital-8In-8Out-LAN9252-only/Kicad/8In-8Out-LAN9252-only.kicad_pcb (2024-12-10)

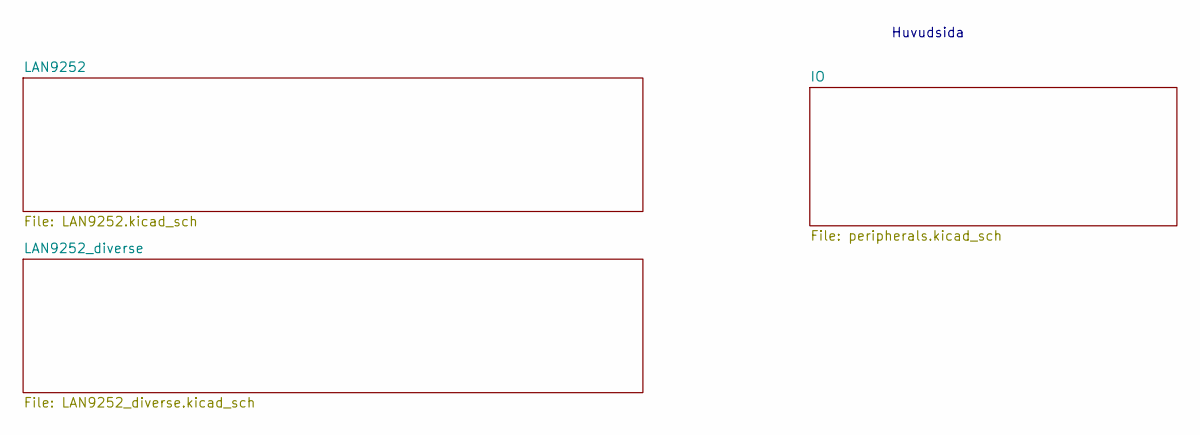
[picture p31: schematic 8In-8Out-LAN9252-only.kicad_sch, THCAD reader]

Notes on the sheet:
Huvudsida

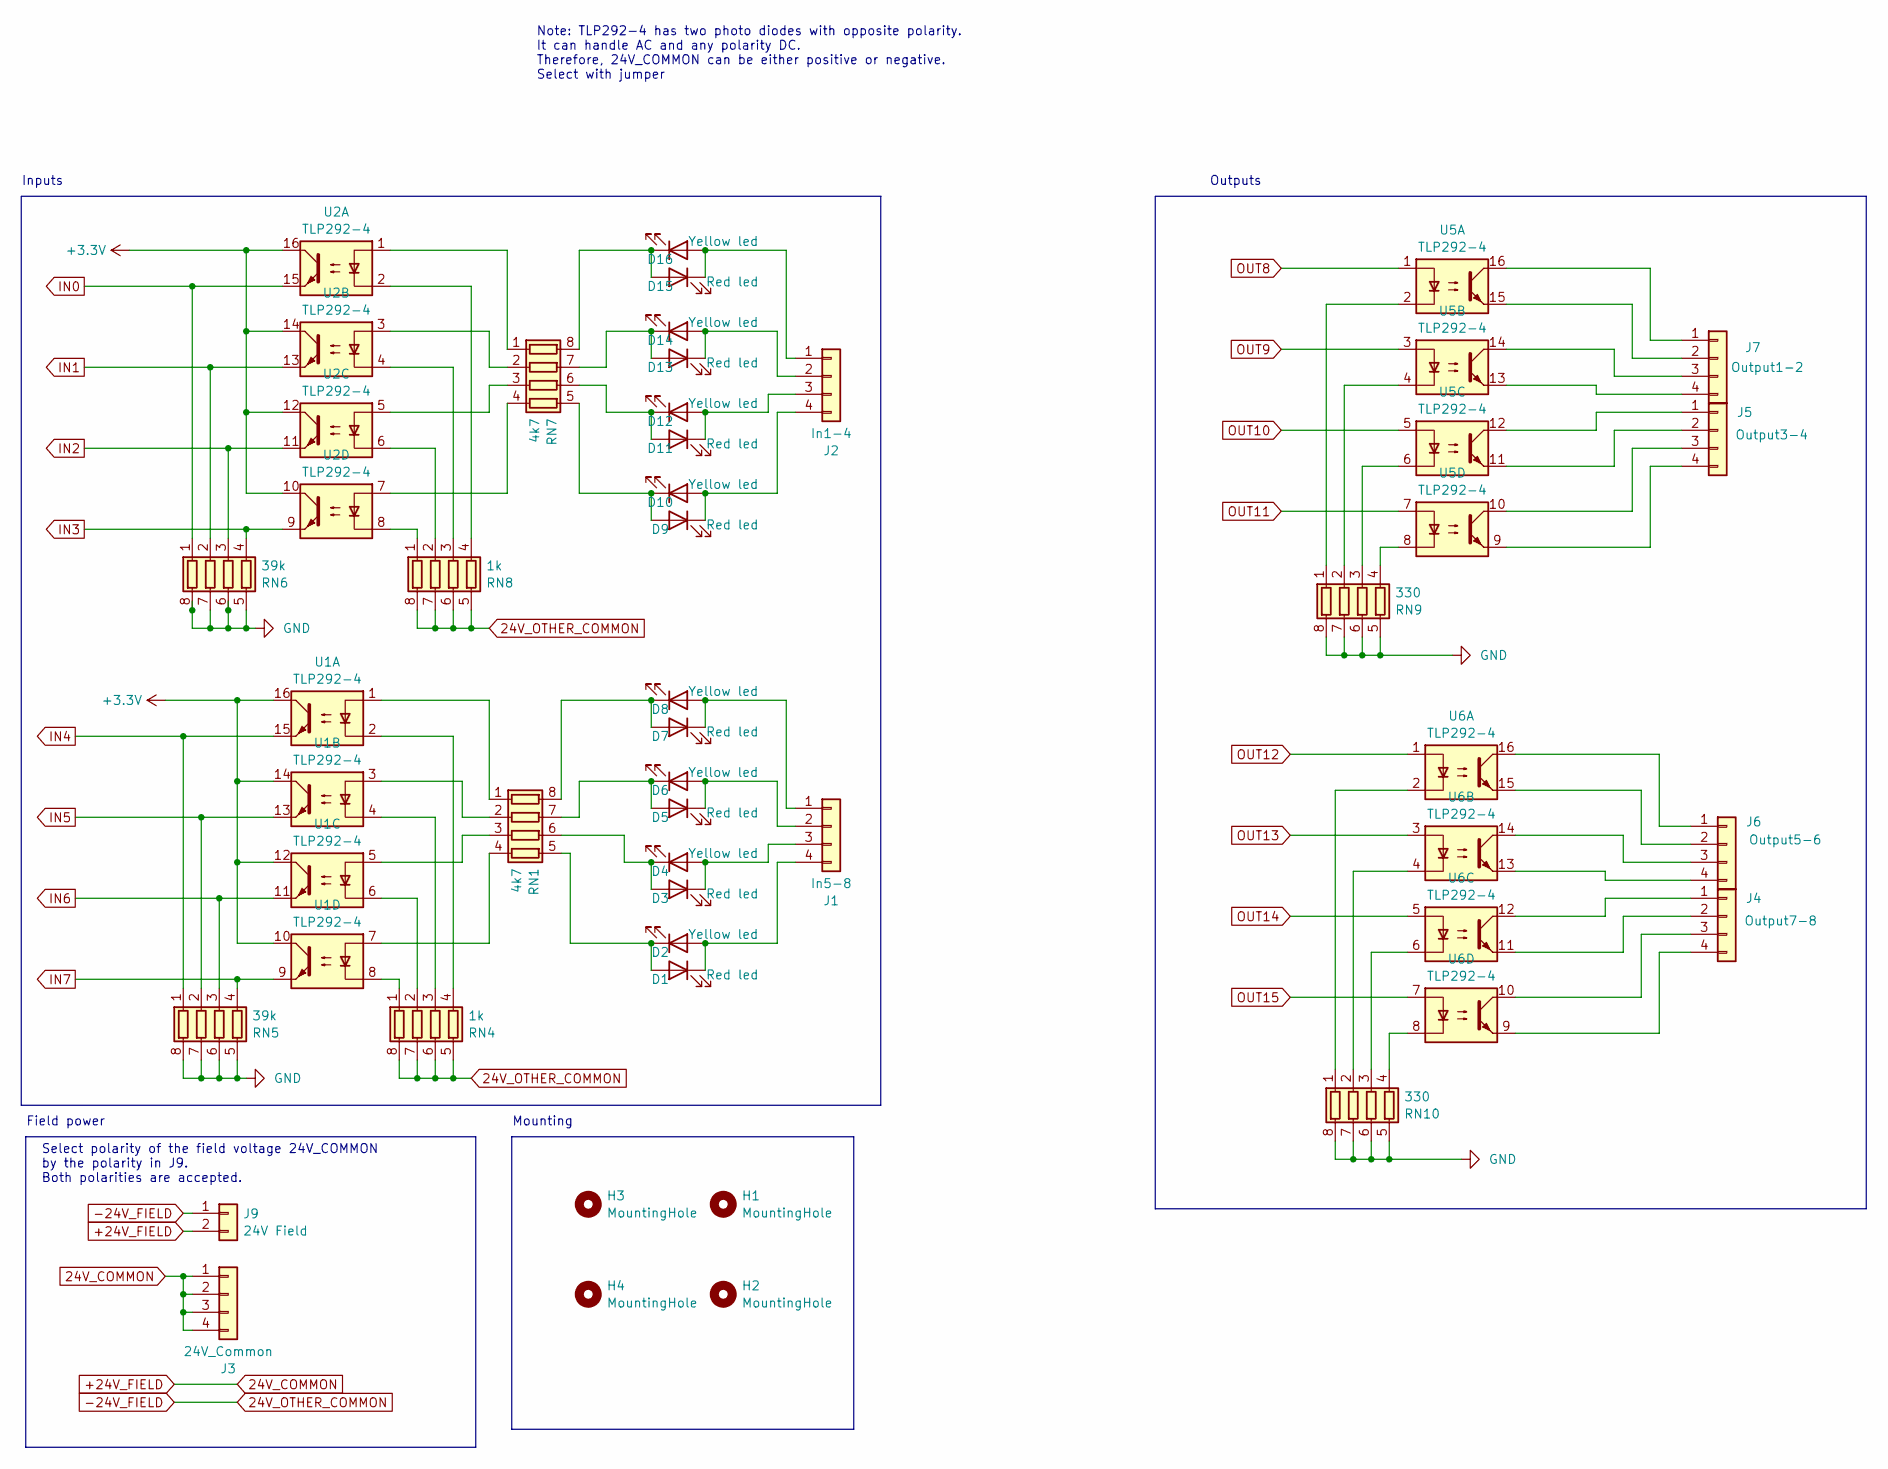
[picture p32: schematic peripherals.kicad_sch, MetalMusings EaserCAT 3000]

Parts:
D1, D3, D5, D7, D9, D11, D13, D15: Red led; LED_0603_1608Metric
D2, D4, D6, D8, D10, D12, D14, D16: Yellow led; LED_0603_1608Metric
H1, H2, H3, H4: MountingHole; MountingHole_3.2mm_M3_ISO14580
J1: In5-8; PhoenixContact_MCV_1,5_4-G-3.5_1x04_P3.50mm_Vertical
J2: In1-4; PhoenixContact_MCV_1,5_4-G-3.5_1x04_P3.50mm_Vertical
J3: 24V_Common; PhoenixContact_MCV_1,5_4-G-3.5_1x04_P3.50mm_Vertical
J4: Output7-8; PhoenixContact_MCV_1,5_4-G-3.5_1x04_P3.50mm_Vertical
J5: Output3-4; PhoenixContact_MCV_1,5_4-G-3.5_1x04_P3.50mm_Vertical
J6: Output5-6; PhoenixContact_MCV_1,5_4-G-3.5_1x04_P3.50mm_Vertical
J7: Output1-2; PhoenixContact_MCV_1,5_4-G-3.5_1x04_P3.50mm_Vertical
J9: 24V Field; PhoenixContact_MCV_1,5_2-G-3.5_1x02_P3.50mm_Vertical
RN1, RN7: 4k7; R_Array_Convex_4x0603
RN4, RN8: 1k; R_Array_Convex_4x0603
RN5, RN6: 39k; R_Array_Convex_4x0603
RN9, RN10: 330; R_Array_Convex_4x0603
U1, U2, U5, U6: TLP292-4; SOIC-16_4.55x10.3mm_P1.27mm

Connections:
+3.3V: U1.10, U1.12, U1.14, U1.16, U2.10, U2.12, U2.14, U2.16; also elsewhere on the board
+24V_FIELD: J3.1, J3.2, J3.3, J3.4, J9.2
-24V_FIELD: J9.1, RN4.5 (R4.2), RN4.6 (R3.2), RN4.7 (R2.2), RN4.8 (R1.2), RN8.5 (R4.2), RN8.6 (R3.2), RN8.7 (R2.2), RN8.8 (R1.2)
GND: RN5.5 (R4.2), RN5.6 (R3.2), RN5.7 (R2.2), RN5.8 (R1.2), RN6.5 (R4.2), RN6.6 (R3.2), RN6.7 (R2.2), RN6.8 (R1.2), RN9.5 (R4.2), RN9.6 (R3.2), RN9.7 (R2.2), RN9.8 (R1.2), RN10.5 (R4.2), RN10.6 (R3.2), RN10.7 (R2.2), RN10.8 (R1.2); also elsewhere on the board
IN0: RN6.1 (R1.1), U2.15; also elsewhere on the board
IN1: RN6.2 (R2.1), U2.13; also elsewhere on the board
IN2: RN6.3 (R3.1), U2.11; also elsewhere on the board
IN3: RN6.4 (R4.1), U2.9; also elsewhere on the board
IN4: RN5.1 (R1.1), U1.15; also elsewhere on the board
IN5: RN5.2 (R2.1), U1.13; also elsewhere on the board
IN6: RN5.3 (R3.1), U1.11; also elsewhere on the board
IN7: RN5.4 (R4.1), U1.9; also elsewhere on the board
unnamed: D1.2 (A), D2.1 (K), RN1.5 (R4.2)
unnamed: D1.1 (K), D2.2 (A), J1.4
unnamed: D3.2 (A), D4.1 (K), RN1.6 (R3.2)
unnamed: D3.1 (K), D4.2 (A), J1.3
unnamed: D5.2 (A), D6.1 (K), RN1.7 (R2.2)
unnamed: D5.1 (K), D6.2 (A), J1.2
unnamed: D7.2 (A), D8.1 (K), RN1.8 (R1.2)
unnamed: D7.1 (K), D8.2 (A), J1.1
unnamed: D9.1 (K), D10.2 (A), J2.4
unnamed: D9.2 (A), D10.1 (K), RN7.5 (R4.2)
unnamed: D11.2 (A), D12.1 (K), RN7.6 (R3.2)
unnamed: D11.1 (K), D12.2 (A), J2.3
unnamed: D13.2 (A), D14.1 (K), RN7.7 (R2.2)
unnamed: D13.1 (K), D14.2 (A), J2.2
unnamed: D15.2 (A), D16.1 (K), RN7.8 (R1.2)
unnamed: D15.1 (K), D16.2 (A), J2.1
unnamed: J4.1, U6.12
unnamed: J4.2, U6.11
unnamed: J4.3, U6.10
unnamed: J4.4, U6.9
unnamed: J5.1, U5.12
unnamed: J5.2, U5.11
unnamed: J5.3, U5.10
unnamed: J5.4, U5.9
unnamed: J6.1, U6.16
unnamed: J6.2, U6.15
unnamed: J6.3, U6.14
unnamed: J6.4, U6.13
unnamed: J7.1, U5.16
unnamed: J7.2, U5.15
unnamed: J7.3, U5.14
unnamed: J7.4, U5.13
unnamed: RN1.1 (R1.1), U1.1
unnamed: RN1.2 (R2.1), U1.3
unnamed: RN1.3 (R3.1), U1.5
unnamed: RN1.4 (R4.1), U1.7
unnamed: RN4.1 (R1.1), U1.8
unnamed: RN4.2 (R2.1), U1.6
unnamed: RN4.3 (R3.1), U1.4
unnamed: RN4.4 (R4.1), U1.2
unnamed: RN7.1 (R1.1), U2.1
unnamed: RN7.2 (R2.1), U2.3
unnamed: RN7.3 (R3.1), U2.5
unnamed: RN7.4 (R4.1), U2.7
unnamed: RN8.1 (R1.1), U2.8
unnamed: RN8.2 (R2.1), U2.6
unnamed: RN8.3 (R3.1), U2.4
unnamed: RN8.4 (R4.1), U2.2
unnamed: RN9.1 (R1.1), U5.2
unnamed: RN9.2 (R2.1), U5.4
unnamed: RN9.3 (R3.1), U5.6
unnamed: RN9.4 (R4.1), U5.8
unnamed: RN10.1 (R1.1), U6.2
unnamed: RN10.2 (R2.1), U6.4
unnamed: RN10.3 (R3.1), U6.6
unnamed: RN10.4 (R4.1), U6.8
OUT8: U5.1; also elsewhere on the board
OUT9: U5.3; also elsewhere on the board
OUT10: U5.5; also elsewhere on the board
OUT11: U5.7; also elsewhere on the board
OUT12: U6.1; also elsewhere on the board
OUT13: U6.3; also elsewhere on the board
OUT14: U6.5; also elsewhere on the board
OUT15: U6.7; also elsewhere on the board

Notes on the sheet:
Inputs
Select polarity of the field voltage 24V_COMMON by the polarity in J9. Both polarities are accepted.
Mounting
Outputs
Field power
Note: TLP292-4 has two photo diodes with opposite polarity. It can handle AC and any polarity DC. Therefore, 24V_COMMON can be either positive or negative. Select with jumper


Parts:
B1, B2: BLM18EG221S; C_0805_2012Metric
C1, C2, C3, C4, C5, C7, C9, C11, C12, C13, C16, C17, C18, C20, C22: 0.1uF; C_0805_2012Metric
C19, C21: 10uF; C_0805_2012Metric
CN1, CN2: 10pF; R_Array_Convex_4x0603
CN3, CN4: 0.1uF; R_Array_Convex_4x0603
D18: Blue; LED_0805_2012Metric
IN1: J0011D01BNL; PulseJack JB0011D01BNL
J8: Conn_01x02_Pin; JST_XH_B2B-XH-A_1x02_P2.50mm_Vertical
OUT1: J0011D01BNL; PulseJack JB0011D01BNL
R2, R5, R7, R8, R9: 10k; R_0805_2012Metric
R3, R6: 1k; R_0805_2012Metric
R11, R14: 22; R_0805_2012Metric
R12, R13, R15: 2k; R_0805_2012Metric
RN2, RN3: 49.9 (51); R_Array_Convex_4x0603
U4: AT24CS32-SSHM; SOIC-8_3.9x4.9mm_P1.27mm
U7: AMS1117-3.3; SOT-223-3_TabPin2

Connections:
+1V2: CN4.1 (R1.1), CN4.2 (R2.1), CN4.3 (R3.1), CN4.4 (R4.1); also elsewhere on the board
+3.3V: B1.1, B2.1, C5.1, C7.1, C9.1, C11.1, C12.1, C13.1, C16.1, C17.2, C18.1, C20.1, C21.1, R12.1, R13.1, RN2.1 (R1.1), RN2.2 (R2.1), RN2.3 (R3.1), RN2.4 (R4.1), RN3.1 (R1.1), RN3.2 (R2.1), RN3.3 (R3.1), RN3.4 (R4.1), U4.8 (VCC), U7.2 (VO); also elsewhere on the board
+3.3VA: CN3.1 (R1.1), CN3.2 (R2.1), CN3.3 (R3.1), CN3.4 (R4.1); also elsewhere on the board
+5V: C19.1, C22.1, J8.2, R15.1, U7.3 (VI)
FXLOSA: R8.1; also elsewhere on the board
FXLOSB: R9.1; also elsewhere on the board
FXLOSEN: R7.1; also elsewhere on the board
GND: C1.1, C2.1, C3.2, C4.2, C5.2, C7.2, C9.2, C11.2, C12.2, C13.2, C16.2, C17.1, C18.2, C19.2, C20.2, C21.2, C22.2, CN1.5 (R4.2), CN1.6 (R3.2), CN1.7 (R2.2), CN1.8 (R1.2), CN2.5 (R4.2), CN2.6 (R3.2), CN2.7 (R2.2), CN2.8 (R1.2), CN3.5 (R4.2), CN3.6 (R3.2), CN3.7 (R2.2), CN3.8 (R1.2), CN4.5 (R4.2), CN4.6 (R3.2), CN4.7 (R2.2), CN4.8 (R1.2), D18.1 (K), IN1.8 (CHS_GND), IN1.10, IN1.SH (CHS_GND), J8.1, OUT1.8 (CHS_GND), OUT1.10, OUT1.SH (CHS_GND), R2.2, R5.2, R7.2, R8.2, R9.2, U4.1 (A0), U4.2 (A1), U4.3 (A2), U4.4 (GND), U4.7 (WP), U7.1 (GND); also elsewhere on the board
I2C_SCL: R14.1; also elsewhere on the board
I2C_SDA: R11.1; also elsewhere on the board
LINKACTLED0: R2.1, R3.1; also elsewhere on the board
LINKACTLED1: R5.1, R6.1; also elsewhere on the board
unnamed: D18.2 (A), R15.2
unnamed: IN1.9, R3.2
unnamed: B2.2, C2.2, IN1.4 (TCT), IN1.5 (RCT)
unnamed: OUT1.9, R6.2
unnamed: B1.2, C1.2, OUT1.4 (TCT), OUT1.5 (RCT)
unnamed: R13.2, R14.2, U4.6 (SCL)
unnamed: R11.2, R12.2, U4.5 (SDA)
RXNA: CN2.4 (R4.1), IN1.6 (RD-), RN3.5 (R4.2); also elsewhere on the board
RXNB: CN1.4 (R4.1), OUT1.6 (RD-), RN2.5 (R4.2); also elsewhere on the board
RXPA: CN2.3 (R3.1), IN1.3 (RD+), RN3.6 (R3.2); also elsewhere on the board
RXPB: CN1.3 (R3.1), OUT1.3 (RD+), RN2.6 (R3.2); also elsewhere on the board
TXNA: CN2.2 (R2.1), IN1.2 (TD-), RN3.7 (R2.2); also elsewhere on the board
TXNB: CN1.2 (R2.1), OUT1.2 (TD-), RN2.7 (R2.2); also elsewhere on the board
TXPA: CN2.1 (R1.1), IN1.1 (TD+), RN3.8 (R1.2); also elsewhere on the board
TXPB: CN1.1 (R1.1), OUT1.1 (TD+), RN2.8 (R1.2); also elsewhere on the board
VDD12TX1: C3.1, C4.1; also elsewhere on the board


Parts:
B3, B4, B5, B6, B7: BLM18EG221S; C_0805_2012Metric
C6, C8: 20pF; C_0805_2012Metric
C10: 0.1uF; C_0805_2012Metric
C14: 1uF; C_0805_2012Metric
C15: 470pF; C_0805_2012Metric
D17: Green led; LED_0805_2012Metric
R1: 12.1k; R_0805_2012Metric
R4: 1k; R_0805_2012Metric
R10: 10k; R_0805_2012Metric
U3: LAN9252_PT; TQFP-64-1EP_10x10mm_P0.5mm_EP8x8mm; PARTREV 04-08-15
Y1: 25MHz; Crystal_HC49-4H_Vertical

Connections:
+1V2: B3.1, B7.1, C14.1, C15.1, U3.6 (VDDCR), U3.24 (VDDCR), U3.38 (VDDCR); also elsewhere on the board
+3.3V: B4.1, B5.1, B6.1, R4.1, R10.1, U3.5 (VDD33), U3.7 (REG_EN), U3.14 (VDDIO), U3.20 (VDDIO), U3.32 (VDDIO), U3.37 (VDDIO), U3.47 (VDDIO); also elsewhere on the board
+3.3VA: B4.2, B5.2, B6.2, U3.51 (VDD33TXRX1), U3.58 (VDD33BIAS), U3.64 (VDD33TXRX2); also elsewhere on the board
FXLOSA: U3.9 (FXSDA/FXLOSA/~FXSDENA); also elsewhere on the board
FXLOSB: U3.10 (FXSDB/FXLOSB/~FXSDENB); also elsewhere on the board
FXLOSEN: U3.8 (~FXLOSEN); also elsewhere on the board
GND: C6.1, C8.1, C10.1, C14.2, C15.2, R1.1, U3.4 (OSCVSS), U3.41 (TESTMODE), U3.65 (VSS); also elsewhere on the board
I2C_SCL: U3.43 (EESCL/TCK); also elsewhere on the board
I2C_SDA: U3.42 (EESDA/TMS); also elsewhere on the board
IN0: U3.36 (D6/AD6/DIGIO0/GPI0/GPO0/MII_RXCLK); also elsewhere on the board
IN1: U3.39 (D7/AD7/DIGIO1/GPI1/GPO1/MII_MDC); also elsewhere on the board
IN2: U3.40 (D8/AD8/DIGIO2/GPI2/GPO2/MII_MDIO); also elsewhere on the board
IN3: U3.49 (D4/AD4/DIGIO3/GPI3/GPO3/MII_LINK); also elsewhere on the board
IN4: U3.23 (D10/AD10/DIGIO4/GPI4/GPO4/MII_TXEN); also elsewhere on the board
IN5: U3.22 (D11/AD11/DIGIO5/GPI5/GPO5/MII_TXD0); also elsewhere on the board
IN6: U3.21 (D12/AD12/DIGIO6/GPI6/GPO6/MII_TXD1); also elsewhere on the board
IN7: U3.16 (D13/AD13/DIGIO7/GPI7/GPO7/MII_TXD2/~TX_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); also elsewhere on the board
LINKACTLED0: U3.48 (LINKACTLED0/TDO/~CHIP_MODE0); also elsewhere on the board
LINKACTLED1: U3.46 (LINKACTLED1/TDI/~CHIP_MODE1); also elsewhere on the board
unnamed: D17.2 (A), R4.2
unnamed: D17.1 (K), U3.45 (RUNLED/~E2PSIZE)
unnamed: C6.2, U3.1 (OSCI), Y1.2
unnamed: C8.2, U3.2 (OSCO), Y1.1
unnamed: R1.2, U3.57 (RBIAS)
unnamed: C10.2, R10.2, U3.11 (~RST)
OUT8: U3.15 (D14/AD14/DIGIO8/GPI8/GPO8/MII_TXD3/~TX_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); also elsewhere on the board
OUT9: U3.33 (A0/D15/AD15/DIGIO9/GPI9/GPO9/MII_RXER); also elsewhere on the board
OUT10: U3.29 (A2/ALEHI/DIGIO10/GPI10/GPO10/LINKACTLED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); also elsewhere on the board
OUT11: U3.26 (A3/DIGIO11/GPI11/GPO11/MII_RXDV); also elsewhere on the board
OUT12: U3.27 (A4/DIGIO12/GPI12/GPO12/MII_RXD0); also elsewhere on the board
OUT13: U3.28 (CS/DIGIO13/GPI13/GPO13/MII_RXD1); also elsewhere on the board
OUT14: U3.30 (WR/ENB/DIGIO14/GPI14/GPO14/MII_RXD2); also elsewhere on the board
OUT15: U3.31 (RD/RD_WR/DIGIO15/GPI15/GPO15/MII_RXD3); also elsewhere on the board
RXNA: U3.54 (RXNA); also elsewhere on the board
RXNB: U3.61 (RXNB); also elsewhere on the board
RXPA: U3.55 (RXPA); also elsewhere on the board
RXPB: U3.60 (RXPB); also elsewhere on the board
TXNA: U3.52 (TXNA); also elsewhere on the board
TXNB: U3.63 (TXNB); also elsewhere on the board
TXPA: U3.53 (TXPA); also elsewhere on the board
TXPB: U3.62 (TXPB); also elsewhere on the board
VDD12TX1: B3.2, B7.2, U3.56 (VDD12TX1), U3.59 (VDD12TX2); also elsewhere on the board


Board: 2 copper layers, 89.2 x 58.9 mm, 99 parts (0 on the bottom side), 108 nets.

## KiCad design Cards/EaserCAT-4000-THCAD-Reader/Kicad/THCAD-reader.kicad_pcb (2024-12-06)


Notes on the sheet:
Huvudsida


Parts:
C48: 0.1uF; C_0805_2012Metric
H1, H2, H3: MountingHole; MountingHole_3.2mm_M3
J1: THCAD; PhoenixContact_MCV_1,5_4-G-3.5_1x04_P3.50mm_Vertical
R1: 120; R_0805_2012Metric
U1: MAX3485CSA/ESA; SO-8_3.9x4.9mm_P1.27mm

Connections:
+3.3V: C48.1, U1.8 (VCC); also elsewhere on the board
+5V: J1.1; also elsewhere on the board
GND: C48.2, J1.4, U1.2 (~RE), U1.3 (DE), U1.5 (GND); also elsewhere on the board
unnamed: J1.2, R1.2, U1.7 (B)
unnamed: J1.3, R1.1, U1.6 (A)
THCAD_CTR: U1.1 (RO); also elsewhere on the board

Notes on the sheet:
Plasma arc voltage frequency counter
Mounting & assembly

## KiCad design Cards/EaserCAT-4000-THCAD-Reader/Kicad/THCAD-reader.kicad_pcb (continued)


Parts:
B1, B2: BLM18EG221S; C_0805_2012Metric
B3, B4, B5, B6, B7: BLM18EG221SN1D; C_0805_2012Metric
C1, C6, C8, C12, C13, C14, C15, C16, C17, C24, C25, C26, C27, C28, C32, C33, C35, C36, C37, C38, C40: 0.1uF; C_0805_2012Metric
C2, C3, C4, C5, C7, C9, C10, C11: 10pF; C_0805_2012Metric
IN1: J0011D01BNL; PulseJack JB0011D01BNL
OUT1: J0011D01BNL; PulseJack JB0011D01BNL
R2, R3: 1k; R_0805_2012Metric
R4, R5, R6, R7, R8, R9, R10, R11: 49.9; R_0805_2012Metric
R14, R15, R18, R19, R20: 10k; R_0805_2012Metric
R17, R29: 22; R_0805_2012Metric
R27, R28: 2k; R_0805_2012Metric
U3: AT24CS32-SSHM; SOIC-8_3.9x4.9mm_P1.27mm

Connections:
+1V2: B6.1, B7.1, C14.1, C25.1, C27.1, C33.1; also elsewhere on the board
+3.3V: B1.1, B2.1, B3.1, B4.1, B5.1, C1.1, C24.1, C26.1, C28.1, C35.1, C36.1, C37.2, C38.1, C40.1, R4.2, R5.2, R6.2, R7.2, R8.2, R9.2, R10.2, R11.2, R27.1, R28.1, U3.8 (VCC); also elsewhere on the board
+3.3VA: B3.2, B4.2, B5.2, C12.1, C16.1, C17.1, C32.1; also elsewhere on the board
FXLOSA: R18.1; also elsewhere on the board
FXLOSB: R19.1; also elsewhere on the board
FXLOSEN: R20.1; also elsewhere on the board
GND: C1.2, C2.1, C3.1, C4.1, C5.1, C6.1, C7.1, C8.1, C9.1, C10.1, C11.1, C12.2, C13.2, C14.2, C15.2, C16.2, C17.2, C24.2, C25.2, C26.2, C27.2, C28.2, C32.2, C33.2, C35.2, C36.2, C37.1, C38.2, C40.2, IN1.8 (CHS_GND), IN1.10, IN1.SH (CHS_GND), OUT1.8 (CHS_GND), OUT1.10, OUT1.SH (CHS_GND), R14.2, R15.2, R18.2, R19.2, R20.2, U3.1 (A0), U3.2 (A1), U3.3 (A2), U3.4 (GND), U3.7 (WP); also elsewhere on the board
GPIO0: R3.1, R14.1; also elsewhere on the board
GPIO1: R2.1, R15.1; also elsewhere on the board
I2C_SCL: R17.1; also elsewhere on the board
I2C_SDA: R29.1; also elsewhere on the board
unnamed: IN1.9, R3.2
unnamed: B1.2, C6.2, IN1.4 (TCT), IN1.5 (RCT)
unnamed: OUT1.9, R2.2
unnamed: B2.2, C8.2, OUT1.4 (TCT), OUT1.5 (RCT)
unnamed: R17.2, R27.2, U3.6 (SCL)
unnamed: R28.2, R29.2, U3.5 (SDA)
RXNA: C5.2, IN1.6 (RD-), R4.1; also elsewhere on the board
RXNB: C7.2, OUT1.6 (RD-), R8.1; also elsewhere on the board
RXPA: C2.2, IN1.3 (RD+), R9.1; also elsewhere on the board
RXPB: C9.2, OUT1.3 (RD+), R5.1; also elsewhere on the board
TXNA: C3.2, IN1.2 (TD-), R10.1; also elsewhere on the board
TXNB: C10.2, OUT1.2 (TD-), R6.1; also elsewhere on the board
TXPA: C4.2, IN1.1 (TD+), R11.1; also elsewhere on the board
TXPB: C11.2, OUT1.1 (TD+), R7.1; also elsewhere on the board
VDD12TX1: B6.2, B7.2, C13.1, C15.1; also elsewhere on the board


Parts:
C18: 470pF; C_0805_2012Metric
C20: 1uF; C_0805_2012Metric
C22, C23: 20pF; C_0805_2012Metric
C30: 0.1uF; C_0805_2012Metric
D1: Green led; LED_0805_2012Metric
R12: 1k; R_0805_2012Metric
R16: 12.1k; R_0805_2012Metric
R21: 10k; R_0805_2012Metric
R22, R31, R32, R33, R35, R36, R38: 22; R_0805_2012Metric
U2: LAN9252_PT; TQFP-64-1EP_10x10mm_P0.5mm_EP8x8mm; PARTREV 04-08-15
Y1: 25MHz; Crystal_HC49-4H_Vertical

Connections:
+1V2: C18.1, C20.1, U2.6 (VDDCR), U2.24 (VDDCR), U2.38 (VDDCR); also elsewhere on the board
+3.3V: R12.1, R21.1, U2.5 (VDD33), U2.7 (REG_EN), U2.14 (VDDIO), U2.20 (VDDIO), U2.32 (VDDIO), U2.37 (VDDIO), U2.47 (VDDIO); also elsewhere on the board
+3.3VA: U2.51 (VDD33TXRX1), U2.58 (VDD33BIAS), U2.64 (VDD33TXRX2); also elsewhere on the board
FXLOSA: U2.9 (FXSDA/FXLOSA/~FXSDENA); also elsewhere on the board
FXLOSB: U2.10 (FXSDB/FXLOSB/~FXSDENB); also elsewhere on the board
FXLOSEN: U2.8 (~FXLOSEN); also elsewhere on the board
GND: C18.2, C20.2, C22.1, C23.1, C30.1, R16.1, U2.4 (OSCVSS), U2.41 (TESTMODE), U2.65 (VSS); also elsewhere on the board
GPIO0: U2.48 (LINKACTLED0/TDO/~CHIP_MODE0); also elsewhere on the board
GPIO1: U2.46 (LINKACTLED1/TDI/~CHIP_MODE1); also elsewhere on the board
I2C_SCL: U2.43 (EESCL/TCK); also elsewhere on the board
I2C_SDA: U2.42 (EESDA/TMS); also elsewhere on the board
IRQ: R33.1; also elsewhere on the board
unnamed: D1.2 (A), R12.2
unnamed: D1.1 (K), U2.45 (RUNLED/~E2PSIZE)
unnamed: R35.2, U2.17 (D0/AD0/WD_STATE/SI/SIO0)
unnamed: R31.2, U2.13 (D1/AD1/EOF/SO/SIO1)
unnamed: R32.2, U2.50 (D5/AD5/OUTVALID/SCS#)
unnamed: R38.2, U2.19 (D9/AD9/LATCH_IN/SCK)
unnamed: R33.2, U2.44 (IRQ)
unnamed: C22.2, U2.1 (OSCI), Y1.2
unnamed: C23.2, U2.2 (OSCO), Y1.1
unnamed: R16.2, U2.57 (RBIAS)
unnamed: R36.1, U2.34 (SYNC0/LATCH0)
unnamed: R22.1, U2.18 (SYNC1/LATCH1)
unnamed: C30.2, R21.2, U2.11 (~RST)
RXNA: U2.54 (RXNA); also elsewhere on the board
RXNB: U2.61 (RXNB); also elsewhere on the board
RXPA: U2.55 (RXPA); also elsewhere on the board
RXPB: U2.60 (RXPB); also elsewhere on the board
SPI_CS: R32.1; also elsewhere on the board
SPI_MISO: R31.1; also elsewhere on the board
SPI_MOSI: R35.1; also elsewhere on the board
SPI_SCK: R38.1; also elsewhere on the board
SYNC0: R36.2; also elsewhere on the board
SYNC1: R22.2; also elsewhere on the board
TXNA: U2.52 (TXNA); also elsewhere on the board
TXNB: U2.63 (TXNB); also elsewhere on the board
TXPA: U2.53 (TXPA); also elsewhere on the board
TXPB: U2.62 (TXPB); also elsewhere on the board
VDD12TX1: U2.56 (VDD12TX1), U2.59 (VDD12TX2); also elsewhere on the board


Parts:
C19, C21, C29, C31, C41, C43, C44, C45, C47, C51, C52, C53, C54, C55, C56: 0.1uF; C_0805_2012Metric
C34, C39: 2.2uF; C_0805_2012Metric
C42, C46: 10uF; C_0805_2012Metric
C49, C50: 22pF; C_0805_2012Metric
D2: Red led; LED_0805_2012Metric
D3: Orange led; LED_0805_2012Metric
D4: Green led; LED_0805_2012Metric
D5, D6, D7: Blue led; LED_0805_2012Metric
J2: Conn_01x02_Pin; JST_XH_B2B-XH-A_1x02_P2.50mm_Vertical
J3: STLINK; JST_XH_B4B-XH-A_1x04_P2.50mm_Vertical
J4: Serial usart1; JST_XH_B4B-XH-A_1x04_P2.50mm_Vertical
R13, R34, R39: 1k; R_0805_2012Metric
R23, R24, R25, R26: 510; R_0805_2012Metric
R30, R37: 22; R_0805_2012Metric
SW1: SW_Push; SW_Push_1P1T_XKB_TS-1187A
U4: STM32F407VGT6; LQFP-100_14x14mm_P0.5mm
U5: AMS1117-3.3; SOT-223-3_TabPin2
Y2: 8 MHz; Crystal_HC49-4H_Vertical

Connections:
+3.3V: C21.1, C29.1, C31.1, C41.1, C44.1, C45.1, C46.1, C47.1, C51.1, C52.1, C53.1, C54.1, C55.1, C56.1, J3.1, R13.2, R34.2, U4.6 (VBAT), U4.11 (VDD), U4.19 (VDD), U4.21 (VREF+), U4.22 (VDDA), U4.28 (VDD), U4.50 (VDD), U4.75 (VDD), U4.100 (VDD), U5.2 (VO); also elsewhere on the board
+5V: C42.1, C43.1, J2.2, J4.1, R39.2, U5.3 (VI); also elsewhere on the board
/STM32F4/BOOT1: R30.2, U4.37 (PB2)
GND: C19.1, C21.2, C29.2, C31.2, C34.1, C39.1, C41.2, C42.2, C43.2, C44.2, C45.2, C46.2, C47.2, C49.1, C50.1, C51.2, C52.2, C53.2, C54.2, C55.2, C56.2, D2.1 (K), D3.1 (K), D4.1 (K), D5.1 (K), D6.1 (K), D7.1 (K), J2.1, J3.2, J4.2, R30.1, R37.1, SW1.1, U4.10 (VSS), U4.20 (VSSA), U4.27 (VSS), U4.74 (VSS), U4.99 (VSS), U5.1 (GND); also elsewhere on the board
IRQ: U4.15 (PC0); also elsewhere on the board
NRST: C19.2, R13.1, SW1.2, U4.14 (NRST)
unnamed: D2.2 (A), R24.1
unnamed: D3.2 (A), R25.1
unnamed: D4.2 (A), R26.1
unnamed: D5.2 (A), R23.1
unnamed: D6.2 (A), R34.1
unnamed: D7.2 (A), R39.1
unnamed: R37.2, U4.94 (BOOT0)
unnamed: R26.2, U4.59 (PD12)
unnamed: R25.2, U4.60 (PD13)
unnamed: R24.2, U4.61 (PD14)
unnamed: R23.2, U4.62 (PD15)
unnamed: C49.2, U4.12 (PH0), Y2.2
unnamed: C50.2, U4.13 (PH1), Y2.1
unnamed: C34.2, U4.49 (VCAP_1)
unnamed: C39.2, U4.73 (VCAP_2)
RX: J4.3, U4.69 (PA10)
SPI_CS: U4.33 (PC4); also elsewhere on the board
SPI_MISO: U4.31 (PA6); also elsewhere on the board
SPI_MOSI: U4.32 (PA7); also elsewhere on the board
SPI_SCK: U4.30 (PA5); also elsewhere on the board
SWCLK: J3.3, U4.76 (PA14)
SWDIO: J3.4, U4.72 (PA13)
SYNC0: U4.18 (PC3); also elsewhere on the board
SYNC1: U4.16 (PC1); also elsewhere on the board
THCAD_CTR: U4.23 (PA0); also elsewhere on the board
TX: J4.4, U4.68 (PA9)


Board: 2 copper layers, 89.2 x 58.9 mm, 126 parts (0 on the bottom side), 71 nets.

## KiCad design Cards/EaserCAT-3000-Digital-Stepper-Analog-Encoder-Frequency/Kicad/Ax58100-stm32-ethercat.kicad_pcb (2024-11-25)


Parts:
D1, D3, D5, D7, D9, D11, D13, D15: Yellow led; LED_0603_1608Metric
D2, D4, D6, D8, D10, D12, D14, D16: Red led; LED_0603_1608Metric
J6: In1-4; PhoenixContact_MCV_1,5_4-G-3.5_1x04_P3.50mm_Vertical
J7: In5-8; PhoenixContact_MCV_1,5_4-G-3.5_1x04_P3.50mm_Vertical
J8: Output1-2; PhoenixContact_MCV_1,5_4-G-3.5_1x04_P3.50mm_Vertical
J9: Output3-4; PhoenixContact_MCV_1,5_4-G-3.5_1x04_P3.50mm_Vertical
J12: 24V Field; PhoenixContact_MCV_1,5_2-G-3.5_1x02_P3.50mm_Vertical
J13: DAC; PhoenixContact_MCV_1,5_3-G-3.5_1x03_P3.50mm_Vertical
J14: In_opt1; JST_XH_B6B-XH-A_1x06_P2.50mm_Vertical
J16: In_opt2; JST_XH_B6B-XH-A_1x06_P2.50mm_Vertical
J18: Out_opt; JST_XH_B6B-XH-A_1x06_P2.50mm_Vertical
R2, R3, R4, R5, R6, R7, R8, R9: 4k7; R_0603_1608Metric
R11, R14, R16, R27: 330; R_0603_1608Metric
R19, R20, R21, R22, R23, R24, R25, R26: 1k; R_0603_1608Metric
R30, R31, R32, R33, R34, R35, R36, R37: 39k; R_0603_1608Metric
U3, U4, U5: TLP292-4; SOIC-16_4.55x10.3mm_P1.27mm

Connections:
+3.3V: J13.1, U4.10, U4.12, U4.14, U4.16, U5.10, U5.12, U5.14, U5.16; also elsewhere on the board
+5V: J14.1, J16.1, J18.1; also elsewhere on the board
+24V_FIELD: J12.2
-24V_FIELD: J12.1, R19.2, R20.2, R21.2, R22.2, R23.2, R24.2, R25.2, R26.2
DAC1: J13.2; also elsewhere on the board
GND: J13.3, J14.6, J16.6, J18.6, R11.2, R14.2, R16.2, R27.2, R30.2, R31.2, R32.2, R33.2, R34.2, R35.2, R36.2, R37.2; also elsewhere on the board
IO1: J18.2, U3.1; also elsewhere on the board
IO2: J18.3, U3.3; also elsewhere on the board
IO3: J18.4, U3.5; also elsewhere on the board
IO4: J18.5, U3.7; also elsewhere on the board
IO5: J14.2, R30.1, U4.15; also elsewhere on the board
IO6: J14.3, R31.1, U4.13; also elsewhere on the board
IO7: J14.4, R32.1, U4.11; also elsewhere on the board
IO8: J14.5, R33.1, U4.9; also elsewhere on the board
IO9: J16.2, R34.1, U5.15; also elsewhere on the board
IO10: J16.3, R35.1, U5.13; also elsewhere on the board
IO11: J16.4, R36.1, U5.11; also elsewhere on the board
IO12: J16.5, R37.1, U5.9; also elsewhere on the board
unnamed: D1.2 (A), D2.1 (K), J6.1
unnamed: D1.1 (K), D2.2 (A), R2.1
unnamed: D3.2 (A), D4.1 (K), J6.2
unnamed: D3.1 (K), D4.2 (A), R3.1
unnamed: D5.2 (A), D6.1 (K), J6.3
unnamed: D5.1 (K), D6.2 (A), R4.1
unnamed: D7.2 (A), D8.1 (K), J6.4
unnamed: D7.1 (K), D8.2 (A), R5.1
unnamed: D9.1 (K), D10.2 (A), R6.1
unnamed: D9.2 (A), D10.1 (K), J7.1
unnamed: D11.2 (A), D12.1 (K), J7.2
unnamed: D11.1 (K), D12.2 (A), R7.1
unnamed: D13.2 (A), D14.1 (K), J7.3
unnamed: D13.1 (K), D14.2 (A), R8.1
unnamed: D15.2 (A), D16.1 (K), J7.4
unnamed: D15.1 (K), D16.2 (A), R9.1
unnamed: J8.1, U3.16
unnamed: J8.2, U3.15
unnamed: J8.3, U3.14
unnamed: J8.4, U3.13
unnamed: J9.1, U3.12
unnamed: J9.2, U3.11
unnamed: J9.3, U3.10
unnamed: J9.4, U3.9
unnamed: R2.2, U4.7
unnamed: R3.2, U4.5
unnamed: R4.2, U4.3
unnamed: R5.2, U4.1
unnamed: R6.2, U5.7
unnamed: R7.2, U5.5
unnamed: R8.2, U5.3
unnamed: R9.2, U5.1
unnamed: R11.1, U3.8
unnamed: R14.1, U3.6
unnamed: R16.1, U3.4
unnamed: R19.1, U4.8
unnamed: R20.1, U4.6
unnamed: R21.1, U4.4
unnamed: R22.1, U4.2
unnamed: R23.1, U5.8
unnamed: R24.1, U5.6
unnamed: R25.1, U5.4
unnamed: R26.1, U5.2
unnamed: R27.1, U3.2

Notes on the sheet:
Inputs
Note the reverse order of inputs 1-4 and pins IO12-IO9
Note the reverse order of inputs 1-4 and pins IO8-IO5
Outputs


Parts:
B1, B4, B5, B6, B7: BLM18EG221SN1D; C_0805_2012Metric
B2, B3: BLM18EG221S; C_0805_2012Metric
C28, C33, C43, C44: 0.1uF; C_0805_2012Metric
C29, C30, C31, C32, C34, C35, C36, C37: 10pF; C_0805_2012Metric
C41, C42: 10uF; C_0805_2012Metric
D19, D21: Green led; LED_0603_1608Metric
D20: Red led; LED_0603_1608Metric
IN1: J0011D01BNL; PulseJack JB0011D01BNL
OUT1: J0011D01BNL; PulseJack JB0011D01BNL
R46, R48, R64, R71: 4k7; R_0805_2012Metric
R49, R50, R51, R52, R53, R54, R55, R56: 49.9; R_0805_2012Metric
R57, R59, R60, R61, R62, R63, R70: 510; R_0805_2012Metric
U9: AMS1117-1.2; SOT-223-3_TabPin2

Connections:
+1V2: B6.1, B7.1, C42.1, C44.1, U9.2 (VO); also elsewhere on the board
+3.3V: B1.1, B2.1, B3.1, B4.1, B5.1, R48.1, R49.2, R50.2, R51.2, R52.2, R53.2, R54.2, R55.2, R56.2, R57.1; also elsewhere on the board
+3.3VA: B1.2, B4.2, B5.2; also elsewhere on the board
+5V: C41.1, C43.1, U9.3 (VI); also elsewhere on the board
A1V2: B6.2, B7.2; also elsewhere on the board
EEP_DONE: D21.2 (A), R71.2; also elsewhere on the board
GND: C28.1, C29.1, C30.1, C31.1, C32.1, C33.1, C34.1, C35.1, C36.1, C37.1, C41.2, C42.2, C43.2, C44.2, D20.1 (K), IN1.8 (CHS_GND), IN1.10, IN1.SH (CHS_GND), OUT1.8 (CHS_GND), OUT1.10, OUT1.SH (CHS_GND), R46.1, R60.2, R62.2, R64.1, R70.1, R71.1, U9.1 (GND); also elsewhere on the board
LED_ERR: R63.1, R64.2; also elsewhere on the board
LED_RUN: D19.1 (K), R48.2; also elsewhere on the board
unnamed: D19.2 (A), R57.2
unnamed: D20.2 (A), R63.2
unnamed: D21.1 (K), R70.2
unnamed: IN1.9, R61.2
unnamed: B3.2, C33.2, IN1.4 (TCT), IN1.5 (RCT)
unnamed: OUT1.9, R59.2
unnamed: B2.2, C28.2, OUT1.4 (TCT), OUT1.5 (RCT)
P0_ACT: R61.1, R62.1; also elsewhere on the board
P0_RXIN: C34.2, IN1.6 (RD-), R53.1; also elsewhere on the board
P0_RXIP: C35.2, IN1.3 (RD+), R54.1; also elsewhere on the board
P0_TXON: C36.2, IN1.2 (TD-), R55.1; also elsewhere on the board
P0_TXOP: C37.2, IN1.1 (TD+), R56.1; also elsewhere on the board
P1_ACT: R59.1, R60.1; also elsewhere on the board
P1_RXIN: C29.2, OUT1.6 (RD-), R49.1; also elsewhere on the board
P1_RXIP: C30.2, OUT1.3 (RD+), R50.1; also elsewhere on the board
P1_TXON: C31.2, OUT1.2 (TD-), R51.1; also elsewhere on the board
P1_TXOP: C32.2, OUT1.1 (TD+), R52.1; also elsewhere on the board
PDI_EMU: R46.2; also elsewhere on the board

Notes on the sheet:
PDI_EMU=0, External MCU control (default) PDI_EMU=1, Ethercat Master Control
I2C EEPROM Size (LED_RUN/EEP_SIZE) 0: 1 Kbit to 16 Kbit (24C16) => Not NC mounted 1: 32 Kbit 24C32 to 4 Mbit => NC mounted
ESC port number (LED_ERR/3PORT_MODE) 0: 2 ports mode => not NC mounted 1: 3 ports mode => NC mounted
Loaded EEPROM Done LED

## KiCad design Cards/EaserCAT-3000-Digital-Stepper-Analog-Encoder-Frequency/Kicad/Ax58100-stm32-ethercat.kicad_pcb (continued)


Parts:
C16, C20, C21, C22, C23, C24, C25, C27, C39, C40, C46, C47, C48, C49, C50: 0.1uF; C_0805_2012Metric
C45: 1uF; C_0805_2012Metric
C51, C52: 18pF; C_0805_2012Metric
R41, R44, R45, R65, R67, R68, R69: 4k7; R_0805_2012Metric
R42: 4k7; R_0603_1608Metric
R43, R47, R58: 22; R_0805_2012Metric
R66: 12k 1%; R_0805_2012Metric
SW1: SW PB; SW_Push_1P1T_XKB_TS-1187A
U8: 24LC32A; SOIC-8_3.9x4.9mm_P1.27mm
U10: AX58100; LQFP-80-1EP_10x10mm_P0.4mm_EP5.3x4.5mm_ThermalVias
Y2: NXK25.000AE12F-KAB6-12; Crystal_SMD_SeikoEpson_TSX3225-4Pin_3.2x2.5mm

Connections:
+1V2: C16.1, C21.1, C24.1, C27.1, C39.1, C48.1, U10.5 (VCCK), U10.16 (VCCK), U10.29 (VCCK), U10.46 (VCCK), U10.55 (VCCK), U10.72 (VCCK); also elsewhere on the board
+3.3V: C20.1, C22.2, C23.1, C25.1, C40.1, R42.2, R44.1, R45.1, R67.2, U8.8 (VCC), U10.10 (VCC3IO), U10.45 (VCC3IO), U10.65 (VCC3IO), U10.77 (VCC3IO); also elsewhere on the board
+3.3VA: C46.1, C47.1, C49.1, C50.1, U10.22 (VCC33A), U10.28 (VCC33A), U10.32 (VCC33A), U10.39 (VCC33A); also elsewhere on the board
A1V2: U10.54 (VCC12A_PLL); also elsewhere on the board
EEP_DONE: U10.21 (EEP_DONE); also elsewhere on the board
GND: C16.2, C20.2, C21.2, C22.1, C23.2, C24.2, C25.2, C27.2, C39.2, C40.2, C45.2, C46.2, C47.2, C48.2, C49.2, C50.2, C51.2, C52.2, R41.2, R58.2, R65.2, R66.2, R68.1, R69.2, SW1.1, U8.1 (A0), U8.2 (A1), U8.3 (A2), U8.4 (GND), U10.56 (FM), U10.81 (GND_EPAD), Y2.2, Y2.4; also elsewhere on the board
I2C_SCL: R44.2, R47.1, U8.6 (SCL)
I2C_SDA: R45.2, U8.5 (SDA), U10.63 (I2C_SDA)
LED_ERR: U10.20 (LED_ERR); also elsewhere on the board
LED_RUN: U10.19 (LED_RUN); also elsewhere on the board
unnamed: R41.1, U8.7 (WP)
unnamed: R47.2, U10.62 (I2C_SCL)
unnamed: R69.1, U10.34 (P0_SD)
unnamed: R65.1, U10.27 (P1_SD)
unnamed: R66.1, U10.33 (RESET_BG)
unnamed: R43.2, U10.6 (SPI_MISO)
unnamed: R58.1, U10.59 (TEST)
P0_ACT: U10.40 (P0_ACT); also elsewhere on the board
P0_RXIN: U10.35 (P0_RXIN); also elsewhere on the board
P0_RXIP: U10.36 (P0_RXIP); also elsewhere on the board
P0_TXON: U10.37 (P0_TXON); also elsewhere on the board
P0_TXOP: U10.38 (P0_TXOP); also elsewhere on the board
P1_ACT: U10.41 (P1_ACT); also elsewhere on the board
P1_RXIN: U10.26 (P1_RXIN); also elsewhere on the board
P1_RXIP: U10.25 (P1_RXIP); also elsewhere on the board
P1_TXON: U10.24 (P1_TXON); also elsewhere on the board
P1_TXOP: U10.23 (P1_TXOP); also elsewhere on the board
PDI_EMU: U10.61 (PDI_EMU); also elsewhere on the board
RESET_MCU: C45.1, R67.1, SW1.2, U10.57 (RSTn); also elsewhere on the board
RSTO: R68.2, U10.58 (RSTO)
SCS_FUNC: R42.1, U10.80 (SCS_FUNC); also elsewhere on the board
SINT: U10.1 (SPI_INT); also elsewhere on the board
SPI_CS: U10.79 (SCS_ESC); also elsewhere on the board
SPI_MISO: R43.1; also elsewhere on the board
SPI_MOSI: U10.78 (SPI_MOSI); also elsewhere on the board
SPI_SCK: U10.64 (SPI_CLK); also elsewhere on the board
SYNC0: U10.2 (SYNC_L0); also elsewhere on the board
SYNC1: U10.3 (SYNC_L1); also elsewhere on the board
XSCI: C52.1, U10.31 (XSCI), Y2.1
XSCO: C51.1, U10.30 (XSCO), Y2.3


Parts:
C1, C2, C3: 0.1uF; C_0805_2012Metric
J1: Step1; PhoenixContact_MCV_1,5_3-G-3.5_1x03_P3.50mm_Vertical
J2: Step2; PhoenixContact_MCV_1,5_3-G-3.5_1x03_P3.50mm_Vertical
J3: Step3; PhoenixContact_MCV_1,5_3-G-3.5_1x03_P3.50mm_Vertical
J4: Step4; PhoenixContact_MCV_1,5_3-G-3.5_1x03_P3.50mm_Vertical
J5: THCAD; PhoenixContact_MCV_1,5_4-G-3.5_1x04_P3.50mm_Vertical
J10: Encoder; PhoenixContact_MCV_1,5_5-G-3.5_1x05_P3.50mm_Vertical
R1: 120; R_0805_2012Metric
R12, R15, R18: 1k; R_0805_2012Metric
U1: MAX3485CSA/ESA; SO-8_3.9x4.9mm_P1.27mm
U2: TXS0108EPW; TSSOP-20_4.4x6.5mm_P0.65mm

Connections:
+3.3V: C1.1, C2.1, U1.8 (VCC), U2.2 (VCCA), U2.10 (OE); also elsewhere on the board
+5V: C3.1, J5.1, J10.1, R12.2, R15.2, R18.2, U2.19 (VCCB); also elsewhere on the board
ENC_A: J10.2, R12.1; also elsewhere on the board
ENC_B: J10.3, R15.1; also elsewhere on the board
ENC_Z: J10.4, R18.1; also elsewhere on the board
GND: C1.2, C2.2, C3.2, J1.3, J2.3, J3.3, J4.3, J5.4, J10.5, U1.2 (~RE), U1.3 (DE), U1.5 (GND), U2.11 (GND); also elsewhere on the board
unnamed: J5.2, R1.2, U1.7 (B)
unnamed: J5.3, R1.1, U1.6 (A)
STEP1_DIR: U2.1 (A1); also elsewhere on the board
STEP1_DIR_OUT: J1.1, U2.20 (B1)
STEP1_STEP: U2.3 (A2); also elsewhere on the board
STEP1_STEP_OUT: J1.2, U2.18 (B2)
STEP2_DIR: U2.4 (A3); also elsewhere on the board
STEP2_DIR_OUT: J2.1, U2.17 (B3)
STEP2_STEP: U2.5 (A4); also elsewhere on the board
STEP2_STEP_OUT: J2.2, U2.16 (B4)
STEP3_DIR: U2.6 (A5); also elsewhere on the board
STEP3_DIR_OUT: J3.1, U2.15 (B5)
STEP3_STEP: U2.7 (A6); also elsewhere on the board
STEP3_STEP_OUT: J3.2, U2.14 (B6)
STEP4_DIR: U2.8 (A7); also elsewhere on the board
STEP4_DIR_OUT: J4.1, U2.13 (B7)
STEP4_STEP: U2.9 (A8); also elsewhere on the board
STEP4_STEP_OUT: J4.2, U2.12 (B8)
THCAD_CTR: U1.1 (RO); also elsewhere on the board

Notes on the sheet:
Encoder input incl pullups
Plasma arc voltage frequency counter
Stepper outputs


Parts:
C4, C6, C7, C9, C11, C12, C14, C15, C17, C19, C26: 0.1uF; C_0805_2012Metric
C5, C18: 2.2uF; C_0805_2012Metric
C8, C10: 22pF; C_0805_2012Metric
C13, C38: 10uF; C_0805_2012Metric
D17, D18: Blue led; LED_0603_1608Metric
J11: 5V Power IN; PhoenixContact_MCV_1,5_2-G-3.5_1x02_P3.50mm_Vertical
J15: Serial usart1; JST_XH_B4B-XH-A_1x04_P2.50mm_Vertical
J17: STLINK; JST_XH_B4B-XH-A_1x04_P2.50mm_Vertical
R10, R13, R17, R28: 4k7; R_0805_2012Metric
R29, R40: 22; R_0805_2012Metric
R38, R39: 1k; R_0805_2012Metric
U6: STM32F407VGT6; LQFP-100_14x14mm_P0.5mm
U7: AMS1117-3.3; SOT-223-3_TabPin2
Y1: 8 MHz; Crystal_HC49-4H_Vertical

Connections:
+3.3V: C4.1, C6.1, C7.1, C9.1, C11.1, C12.1, C14.1, C17.1, C19.1, C26.1, C38.1, J17.1, R39.2, U6.6 (VBAT), U6.11 (VDD), U6.19 (VDD), U6.21 (VREF+), U6.22 (VDDA), U6.28 (VDD), U6.50 (VDD), U6.75 (VDD), U6.100 (VDD), U7.2 (VO); also elsewhere on the board
+5V: C13.1, C15.1, J11.2, J15.1, R38.2, U7.3 (VI); also elsewhere on the board
/STM32F4/BOOT1: R40.2, U6.37 (PB2)
DAC1: U6.29 (PA4); also elsewhere on the board
ENC_A: U6.23 (PA0); also elsewhere on the board
ENC_B: U6.24 (PA1); also elsewhere on the board
ENC_Z: U6.26 (PA3); also elsewhere on the board
GND: C4.2, C5.1, C6.2, C7.2, C8.1, C9.2, C10.1, C11.2, C12.2, C13.2, C14.2, C15.2, C17.2, C18.1, C19.2, C26.2, C38.2, D17.1 (K), D18.1 (K), J11.1, J15.2, J17.2, R10.1, R13.1, R17.1, R28.1, R29.1, R40.1, U6.10 (VSS), U6.20 (VSSA), U6.27 (VSS), U6.74 (VSS), U6.99 (VSS), U7.1 (GND); also elsewhere on the board
IO1: U6.34 (PC5); also elsewhere on the board
IO2: U6.35 (PB0); also elsewhere on the board
IO3: U6.36 (PB1); also elsewhere on the board
IO4: U6.38 (PE7); also elsewhere on the board
IO5: U6.39 (PE8); also elsewhere on the board
IO6: U6.40 (PE9); also elsewhere on the board
IO7: U6.41 (PE10); also elsewhere on the board
IO8: U6.42 (PE11); also elsewhere on the board
IO9: U6.43 (PE12); also elsewhere on the board
IO10: U6.44 (PE13); also elsewhere on the board
IO11: U6.45 (PE14); also elsewhere on the board
IO12: U6.46 (PE15); also elsewhere on the board
unnamed: D17.2 (A), R38.1
unnamed: D18.2 (A), R39.1
unnamed: R29.2, U6.94 (BOOT0)
unnamed: C8.2, U6.12 (PH0), Y1.2
unnamed: C10.2, U6.13 (PH1), Y1.1
unnamed: C18.2, U6.49 (VCAP_1)
unnamed: C5.2, U6.73 (VCAP_2)
RESET_MCU: U6.51 (PB12); also elsewhere on the board
RX: J15.3, U6.69 (PA10)
SCS_FUNC: U6.9 (PC15); also elsewhere on the board
SINT: U6.15 (PC0); also elsewhere on the board
SPI_CS: U6.33 (PC4); also elsewhere on the board
SPI_MISO: U6.31 (PA6); also elsewhere on the board
SPI_MOSI: U6.32 (PA7); also elsewhere on the board
SPI_SCK: U6.30 (PA5); also elsewhere on the board
STEP1_DIR: U6.71 (PA12); also elsewhere on the board
STEP1_STEP: R10.2, U6.70 (PA11); also elsewhere on the board
STEP2_DIR: U6.65 (PC8); also elsewhere on the board
STEP2_STEP: R13.2, U6.66 (PC9); also elsewhere on the board
STEP3_DIR: U6.58 (PD11); also elsewhere on the board
STEP3_STEP: R17.2, U6.59 (PD12); also elsewhere on the board
STEP4_DIR: U6.3 (PE4); also elsewhere on the board
STEP4_STEP: R28.2, U6.4 (PE5); also elsewhere on the board
SWCLK: J17.3, U6.76 (PA14)
SWDIO: J17.4, U6.72 (PA13)
SYNC0: U6.18 (PC3); also elsewhere on the board
SYNC1: U6.16 (PC1); also elsewhere on the board
THCAD_CTR: U6.25 (PA2); also elsewhere on the board
TX: J15.4, U6.68 (PA9)

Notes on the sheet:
Timer allocation
Timer 1, ch 4, PA11: Stepgen 1 Timer 2, ch 3,4, PA0,PA1: Encoder Timer 3, ch 4, PC9: Stepgen 2 Timer 4, ch 1, PD12: Stepgen 3 Timer 5, ch 3, PA2: Frequency counter THCAD Timer 6: Not used (Tone) Timer 7: Not used (Servo) Timer 8: Not used, pins collide with tim3 Timer 9, ch 1, PE5: Stepgen 4


Board: 2 copper layers, 94.5 x 74.4 mm, 184 parts (0 on the bottom side), 140 nets.

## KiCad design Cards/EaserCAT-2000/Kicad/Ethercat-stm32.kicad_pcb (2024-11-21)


Board: 4 copper layers, 89.9 x 59.2 mm, 134 parts (0 on the bottom side), 91 nets.

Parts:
B1, B2: BLM18EG221S; C_0805_2012Metric
B3, B4, B5, B6, B7: BLM18EG221SN1D; C_0805_2012Metric
C1, C2: 20pF; C_0805_2012Metric
C3, C14, C15, C16, C17, C18, C19, C20, C21, C22, C23, C24, C25, C26, C27, C28, C29, C30, C32, C33, C34, C35, C37, C38, C39, C40, C42, C43, C44, C45, C46, C47, C48, C50, C51, C52, C54: 0.1uF; C_0805_2012Metric
C4: 470pF; C_0805_2012Metric
C5: 1uF; C_0805_2012Metric
C6, C7, C8, C9, C10, C11, C12, C13: 10pF; C_0805_2012Metric
C41, C49: 10uF; C_0805_2012Metric
C53, C57: 2.2uF; C_0805_2012Metric
C55, C56: 22pF; C_0805_2012Metric
D1: Green led; LED_0805_2012Metric
D2, D3: Blue led; LED_0805_2012Metric
IN1: J0011D01BNL; PulseJack JB0011D01BNL
J1: Conn_01x02_Pin; JST_XH_B2B-XH-A_1x02_P2.50mm_Vertical
J2: Serial usart1; JST_XH_B4B-XH-A_1x04_P2.50mm_Vertical
J3: STLINK; JST_XH_B4B-XH-A_1x04_P2.50mm_Vertical
J4: I2C bus2; PinHeader_1x04_P2.54mm_Vertical
J5: DAC1; JST_XH_B3B-XH-A_1x03_P2.50mm_Vertical
J6: Encoder 1; JST_XH_B5B-XH-A_1x05_P2.50mm_Vertical
J7: Encoder 2; JST_XH_B5B-XH-A_1x05_P2.50mm_Vertical
J8: Encoder 3; JST_XH_B5B-XH-A_1x05_P2.50mm_Vertical
J9: Encoder 4; JST_XH_B5B-XH-A_1x05_P2.50mm_Vertical
J10, J11, J12: Conn_01x06_Pin; JST_XH_B6B-XH-A_1x06_P2.50mm_Vertical
J13: Stepper 1; JST_XH_B4B-XH-A_1x04_P2.50mm_Vertical
J14: Stepper 2; JST_XH_B4B-XH-A_1x04_P2.50mm_Vertical
OUT1: J0011D01BNL; PulseJack JB0011D01BNL
R1, R21, R22, R23, R24, R25: 10k; R_0805_2012Metric
R2: 12.1k; R_0805_2012Metric
R3, R19, R20, R30, R31, R32, R39, R40, R41, R42, R43, R44, R45, R46, R47, R48, R49, R50: 1k; R_0805_2012Metric
R4, R5, R6, R7, R8, R9, R10, R28, R29, R33, R34: 22; R_0805_2012Metric
R11, R12, R13, R14, R15, R16, R17, R18: 49.9; R_0805_2012Metric
R26, R27: 2k; R_0805_2012Metric
SW1: SW_Push; SW_Push_1P1T_XKB_TS-1187A
U1: LAN9252_PT; TQFP-64-1EP_10x10mm_P0.5mm_EP8x8mm
U2: AT24CS32-SSHM; SOIC-8_3.9x4.9mm_P1.27mm
U3: AMS1117-3.3; SOT-223-3_TabPin2
U4: STM32F407VGT6; LQFP-100_14x14mm_P0.5mm
Y1: 25MHz; Crystal_HC49-U_Vertical
Y2: 8 MHz; Crystal_HC49-U_Vertical

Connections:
+1V2: B6.1, B7.1, C4.1, C5.1, C20.1, C25.1, C30.1, C35.1, U1.6 (VDDCR), U1.24 (VDDCR), U1.38 (VDDCR)
+3.3V: B1.1, B2.1, B3.1, B4.1, B5.1, C16.2, C17.1, C18.1, C22.1, C23.1, C27.1, C28.1, C32.1, C33.1, C37.1, C39.1, C40.1, C42.1, C43.1, C44.1, C46.1, C47.1, C48.1, C49.1, C50.1, C51.1, C52.1, C54.1, J3.1, J4.1, J5.1, R1.1, R3.1, R11.2, R12.2, R13.2, R14.2, R15.2, R16.2, R17.2, R18.2, R26.1, R27.1, R31.2, R32.2, R39.2, R40.2, R41.2, R42.2, R43.2, R44.2, R45.2, R46.2, R47.2, R48.2, R49.2, R50.2, U1.5 (VDD33), U1.7 (REG_EN), U1.14 (VDDIO), U1.20 (VDDIO), U1.32 (VDDIO), U1.37 (VDDIO), U1.47 (VDDIO), U2.8 (VCC), U3.2 (VO), U4.6 (VBAT), U4.11 (VDD), U4.19 (VDD), U4.21 (VREF+), U4.22 (VDDA), U4.28 (VDD), U4.50 (VDD), U4.75 (VDD), U4.100 (VDD)
+3.3VA: B3.2, B4.2, B5.2, C19.1, C24.1, C29.1, C34.1, U1.51 (VDD33TXRX1), U1.58 (VDD33BIAS), U1.64 (VDD33TXRX2)
+5V: C38.1, C41.1, J1.2, J2.1, J6.5, J7.5, J8.5, J9.5, J10.1, J11.1, J12.1, J13.1, J14.1, R30.2, U3.3 (VI)
/STM32F4/BOOT1: R34.2, U4.37 (PB2)
DAC1: J5.2, U4.29 (PA4)
ENC1_A: J6.4, R39.1, U4.23 (PA0)
ENC1_B: J6.3, R43.1, U4.24 (PA1)
ENC1_Z: J6.2, R47.1, U4.25 (PA2)
ENC2_A: J7.4, R40.1, U4.90 (PB4)
ENC2_B: J7.3, R44.1, U4.91 (PB5)
ENC2_Z: J7.2, R48.1, U4.92 (PB6)
ENC3_A: J8.4, R41.1, U4.59 (PD12)
ENC3_B: J8.3, R45.1, U4.60 (PD13)
ENC3_Z: J8.2, R49.1, U4.58 (PD11)
ENC4_A: J9.4, R42.1, U4.63 (PC6)
ENC4_B: J9.3, R46.1, U4.64 (PC7)
ENC4_Z: J9.2, R50.1, U4.67 (PA8)
FXLOSA: R21.1, U1.9 (FXSDA/FXLOSA/~FXSDENA)
FXLOSB: R22.1, U1.10 (FXSDB/FXLOSB/~FXSDENB)
FXLOSEN: R23.1, U1.8 (~FXLOSEN)
GND: C1.1, C2.1, C3.1, C4.2, C5.2, C6.1, C7.1, C8.1, C9.1, C10.1, C11.1, C12.1, C13.1, C14.1, C15.1, C16.1, C17.2, C18.2, C19.2, C20.2, C21.2, C22.2, C23.2, C24.2, C25.2, C26.2, C27.2, C28.2, C29.2, C30.2, C32.2, C33.2, C34.2, C35.2, C37.2, C38.2, C39.2, C40.2, C41.2, C42.2, C43.2, C44.2, C45.1, C46.2, C47.2, C48.2, C49.2, C50.2, C51.2, C52.2, C53.1, C54.2, C55.1, C56.1, C57.1, D2.1 (K), D3.1 (K), IN1.8 (CHS_GND), IN1.10, IN1.SH (CHS_GND), J1.1, J2.2, J3.2, J4.4, J5.3, J6.1, J7.1, J8.1, J9.1, J10.6, J11.6, J12.6, J13.4, J14.4, OUT1.8 (CHS_GND), OUT1.10, OUT1.SH (CHS_GND), R2.1, R21.2, R22.2, R23.2, R24.2, R25.2, R33.1, R34.1, SW1.1, U1.4 (OSCVSS), U1.41 (TESTMODE), U1.65 (VSS), U2.1 (A0), U2.2 (A1), U2.3 (A2), U2.4 (GND), U2.7 (WP), U3.1 (GND), U4.10 (VSS), U4.20 (VSSA), U4.27 (VSS), U4.74 (VSS), U4.99 (VSS)
GPIO0: R19.1, R24.1, U1.48 (LINKACTLED0/TDO/~CHIP_MODE0)
GPIO1: R20.1, R25.1, U1.46 (LINKACTLED1/TDI/~CHIP_MODE1)
I2C2_SCL: J4.2, U4.47 (PB10)
I2C2_SDA: J4.3, U4.48 (PB11)
I2C_SCL: R29.1, U1.43 (EESCL/TCK)
I2C_SDA: R28.1, U1.42 (EESDA/TMS)
IO1: J10.2, U4.34 (PC5)
IO2: J10.3, U4.35 (PB0)
IO3: J10.4, U4.36 (PB1)
IO4: J10.5, U4.38 (PE7)
IO5: J11.2, U4.39 (PE8)
IO6: J11.3, U4.40 (PE9)
IO7: J11.4, U4.41 (PE10)
IO8: J11.5, U4.42 (PE11)
IO9: J12.2, U4.43 (PE12)
IO10: J12.3, U4.44 (PE13)
IO11: J12.4, U4.45 (PE14)
IO12: J12.5, U4.46 (PE15)
IRQ: R10.1, U4.15 (PC0)
NRST: C45.2, R32.1, SW1.2, U4.14 (NRST)
unnamed: D1.2 (A), R3.2
unnamed: D1.1 (K), U1.45 (RUNLED/~E2PSIZE)
unnamed: D2.2 (A), R30.1
unnamed: D3.2 (A), R31.1
unnamed: IN1.9, R19.2
unnamed: B1.2, C14.2, IN1.4 (TCT), IN1.5 (RCT)
unnamed: OUT1.9, R20.2
unnamed: B2.2, C15.2, OUT1.4 (TCT), OUT1.5 (RCT)
unnamed: R6.2, U1.17 (D0/AD0/WD_STATE/SI/SIO0)
unnamed: R7.2, U1.13 (D1/AD1/EOF/SO/SIO1)
unnamed: R8.2, U1.50 (D5/AD5/OUTVALID/SCS#)
unnamed: R9.2, U1.19 (D9/AD9/LATCH_IN/SCK)
unnamed: R10.2, U1.44 (IRQ)
unnamed: C1.2, U1.1 (OSCI), Y1.2
unnamed: C2.2, U1.2 (OSCO), Y1.1
unnamed: R2.2, U1.57 (RBIAS)
unnamed: R4.1, U1.34 (SYNC0/LATCH0)
unnamed: R5.1, U1.18 (SYNC1/LATCH1)
unnamed: C3.2, R1.2, U1.11 (~RST)
unnamed: R27.2, R29.2, U2.6 (SCL)
unnamed: R26.2, R28.2, U2.5 (SDA)
unnamed: R33.2, U4.94 (BOOT0)
unnamed: C55.2, U4.12 (PH0), Y2.2
unnamed: C56.2, U4.13 (PH1), Y2.1
unnamed: C53.2, U4.49 (VCAP_1)
unnamed: C57.2, U4.73 (VCAP_2)
RX: J2.3, U4.69 (PA10)
RXNA: C12.2, IN1.6 (RD-), R17.1, U1.54 (RXNA)
RXNB: C13.2, OUT1.6 (RD-), R18.1, U1.61 (RXNB)
RXPA: C10.2, IN1.3 (RD+), R15.1, U1.55 (RXPA)
RXPB: C11.2, OUT1.3 (RD+), R16.1, U1.60 (RXPB)
SPI_CS: R8.1, U4.33 (PC4)
SPI_MISO: R7.1, U4.31 (PA6)
SPI_MOSI: R6.1, U4.32 (PA7)
SPI_SCK: R9.1, U4.30 (PA5)
STEP1_DIR: J13.2, U4.71 (PA12)
STEP1_STEP: J13.3, U4.70 (PA11)
STEP2_DIR: J14.2, U4.78 (PC10)
STEP2_STEP: J14.3, U4.66 (PC9)
SWCLK: J3.3, U4.76 (PA14)
SWDIO: J3.4, U4.72 (PA13)
SYNC0: R4.2, U4.18 (PC3)
SYNC1: R5.2, U4.16 (PC1)
TX: J2.4, U4.68 (PA9)
TXNA: C8.2, IN1.2 (TD-), R13.1, U1.52 (TXNA)
TXNB: C9.2, OUT1.2 (TD-), R14.1, U1.63 (TXNB)
TXPA: C6.2, IN1.1 (TD+), R11.1, U1.53 (TXPA)
TXPB: C7.2, OUT1.1 (TD+), R12.1, U1.62 (TXPB)
VDD12TX1: B6.2, B7.2, C21.1, C26.1, U1.56 (VDD12TX1), U1.59 (VDD12TX2)

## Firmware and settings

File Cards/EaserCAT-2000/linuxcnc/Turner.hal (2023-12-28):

# Generated by PNCconf at Sat Sep 10 10:10:56 2016
# If you make changes to this file, they will be
# overwritten when you run PNCconf again

loadrt [KINS]KINEMATICS
#autoconverted  trivkins
loadrt [EMCMOT]EMCMOT servo_period_nsec=[EMCMOT]SERVO_PERIOD num_joints=[KINS]JOINTS 

loadusr -W lcec_conf ethercat-conf.xml
loadrt lcec
loadrt cia402 count=2
loadrt metalmusings_encoder

addf lcec.read-all            servo-thread
addf cia402.0.read-all        servo-thread
addf cia402.1.read-all        servo-thread
addf metalmusings-encoder.0     servo-thread
addf motion-command-handler   servo-thread
addf motion-controller        servo-thread

#*******************
#  AXIS X
#*******************

# --- joint signals for motion

net x-pos-cmd    <= joint.0.motor-pos-cmd
net x-vel-cmd    <= joint.0.vel-cmd
net x-pos-fb     <= joint.0.motor-pos-fb
net x-enable     <= joint.0.amp-enable-out

# --- connect stepper driver to joint

net x-pos-cmd    => cia402.0.pos-cmd
net x-pos-fb     => cia402.0.pos-fb
net x-enable     => cia402.0.enable

# --- ect60 settings

setp cia402.0.csp-mode 1
setp cia402.0.pos-scale 5000

# --- from stepper(ethercat) to cia402

net x-statusword      lcec.0.4.cia-statusword  => cia402.0.statusword
net x-opmode-display  lcec.0.4.opmode-display  => cia402.0.opmode-display
net x-drv-act-pos     lcec.0.4.actual-position => cia402.0.drv-actual-position
net x-drv-act-velo    lcec.0.4.actual-velocity => cia402.0.drv-actual-velocity

# --- from cia402 to stepper(ethercat) 

net x-controlword         cia402.0.controlword         => lcec.0.4.cia-controlword
net x-modes-of-operation  cia402.0.opmode              => lcec.0.4.opmode
net x-drv-target-pos      cia402.0.drv-target-position => lcec.0.4.target-position
net x-drv-target-velo     cia402.0.drv-target-velocity => lcec.0.4.target-velocity

#*******************
#  AXIS Z
#*******************

# --- joint signals for motion

net z-pos-cmd    <= joint.1.motor-pos-cmd
net z-vel-cmd    <= joint.1.vel-cmd
net z-pos-fb     <= joint.1.motor-pos-fb
net z-enable     <= joint.1.amp-enable-out

# --- connect stepper driver to the joint

net z-pos-cmd    => cia402.1.pos-cmd
net z-pos-fb     => cia402.1.pos-fb
net z-enable     => cia402.1.enable

# --- ect60 settings

setp cia402.1.csp-mode 1
setp cia402.1.pos-scale 2000

# --- from servo(ethercat) to cia402

net z-statusword      lcec.0.5.cia-statusword  => cia402.1.statusword
net z-opmode-display  lcec.0.5.opmode-display  => cia402.1.opmode-display
net z-drv-act-pos     lcec.0.5.actual-position => cia402.1.drv-actual-position
net z-drv-act-velo    lcec.0.5.actual-velocity => cia402.1.drv-actual-velocity

# --- from cia402 to servo(ethercat) 

net z-controlword         cia402.1.controlword         => lcec.0.5.cia-controlword
net z-modes-of-operation  cia402.1.opmode              => lcec.0.5.opmode
net z-drv-target-pos      cia402.1.drv-target-position => lcec.0.5.target-position
net z-drv-target-velo     cia402.1.drv-target-velocity => lcec.0.5.target-velocity

#*********************
#   E-STOP
#*********************

setp iocontrol.0.emc-enable-in 1
#net estop iocontrol.0.emc-enable-in lcec.0.1.din-0

setp lcec.0.3.enc-pos-scale [SPINDLE_9]ENCODER_SCALE
setp lcec.0.6.enc-pos-scale [SPINDLE_9]ENCODER_SCALE

net spindle-revs <= lcec.0.3.enc-pos
net spindle-revs <= lcec.0.6.enc-position
loadrt invert 
loadrt mult2    names=mult2.rps,mult2.rpm
addf   invert.0   servo-thread
addf   mult2.rps  servo-thread
addf   mult2.rpm  servo-thread

setp invert.0.in          [SPINDLE_9]ENCODER_SCALE
setp mult2.rpm.in0        -60.0
setp mult2.rpm.in0        60.0
#net  enc-invert-pos-scale mult2.rps.in0  <= invert.0.out
net  enc-get-freq-rps     mult2.rps.in1  <= lcec.0.3.enc-frequency
#net  spindle-vel-fb-rps   mult2.rpm.in1  <= mult2.rps.out
#net  spindle-vel-fb-rpm   mult2.rpm.out
net  spindle-index-enable lcec.0.3.enc-index-c-enable

net  spindle-vel-fb-rps   mult2.rpm.in1  <= lcec.0.6.enc-frequency
net  spindle-vel-fb-rpm   mult2.rpm.out

net  to_encoder           metalmusings-encoder.0.index-latch-enable lcec.0.6.enc-index-latch-enable
net  from_encoder         metalmusings-encoder.0.index-status       lcec.0.6.index-status
net  spindle-index-enable metalmusings-encoder.0.index-c-enable

# ---setup spindle control signals---

net spindle-vel-cmd-rps        <=  spindle.0.speed-out-rps
net spindle-vel-cmd-rps-abs    <=  spindle.0.speed-out-rps-abs
net spindle-vel-cmd-rpm        <=  spindle.0.speed-out
net spindle-vel-cmd-rpm-abs    <=  spindle.0.speed-out-abs
net spindle-enable             <=  spindle.0.on
net spindle-cw                 <=  spindle.0.forward
net spindle-ccw                <=  spindle.0.reverse
net spindle-brake              <=  spindle.0.brake
net spindle-revs               =>  spindle.0.revs
net spindle-at-speed           =>  spindle.0.at-speed
net spindle-vel-fb-rps         =>  spindle.0.speed-in
net spindle-index-enable      <=>  spindle.0.index-enable


#******************************
# connect miscellaneous signals
#******************************

#  ---HALUI signals---

net joint-select-a        halui.axis.x.select
net x-is-homed            halui.joint.0.is-homed
net jog-x-pos             halui.axis.x.plus
net jog-x-neg             halui.axis.x.minus
net jog-x-analog          halui.axis.x.analog
net joint-select-b        halui.axis.z.select
net z-is-homed            halui.joint.1.is-homed
net jog-z-pos             halui.axis.z.plus
net jog-z-neg             halui.axis.z.minus
net jog-z-analog          halui.axis.z.analog
net jog-selected-pos      halui.axis.selected.plus
net jog-selected-neg      halui.axis.selected.minus
net spindle-manual-cw     halui.spindle.0.forward
net spindle-manual-ccw    halui.spindle.0.reverse
net spindle-manual-stop   halui.spindle.0.stop
net machine-is-on         halui.machine.is-on
net jog-speed             halui.axis.jog-speed 
net MDI-mode              halui.mode.is-mdi

#  ---coolant signals---

net coolant-mist      <=  iocontrol.0.coolant-mist
net coolant-flood     <=  iocontrol.0.coolant-flood

#  ---probe signal---

net probe-in     =>  motion.probe-input

#  ---motion control signals---

net in-position               <=  motion.in-position
net machine-is-enabled        <=  motion.motion-enabled

#  ---digital in / out signals---

#  ---estop signals---

net estop-out     <=  iocontrol.0.user-enable-out
net estop-ext     =>  iocontrol.0.emc-enable-in

#  ---manual tool change signals---

loadusr -W hal_manualtoolchange
#net tool-change-request     iocontrol.0.tool-change       =>  hal_manualtoolchange.change
#net tool-change-confirmed   iocontrol.0.tool-changed      <=  hal_manualtoolchange.changed
#net tool-number             iocontrol.0.tool-prep-number  =>  hal_manualtoolchange.number
#net tool-prepare-loopback   iocontrol.0.tool-prepare      =>  iocontrol.0.tool-prepared

addf cia402.0.write-all       servo-thread
addf cia402.1.write-all       servo-thread
addf lcec.write-all           servo-thread

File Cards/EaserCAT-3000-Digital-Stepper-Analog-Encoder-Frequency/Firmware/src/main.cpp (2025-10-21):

// EaserCAT 3000
#include <Arduino.h>
#include <stdio.h>
extern "C" {
#include "ecat_slv.h"
#include "utypes.h"
};
_Objects Obj;

#include "extend32to64.h"
extend32to64 longTime;
volatile uint64_t irqTime = 0;

HardwareSerial Serial1(PA10, PA9);

////// Digital IO
const byte INPUTS[8] = {PE8, PE9, PE10, PE11, PE12, PE13, PE14, PE15};
const byte OUTPUTS[4] = {PC5, PB0, PB1, PE7};

#define bitset(byte, nbit) ((byte) |= (1 << (nbit)))
#define bitclear(byte, nbit) ((byte) &= ~(1 << (nbit)))
#define bitflip(byte, nbit) ((byte) ^= (1 << (nbit)))
#define bitcheck(byte, nbit) ((byte) & (1 << (nbit)))

///// Analog out
const byte DAC1_pin = PA4;

//////// Stepper generators
#include "StepGen3.h"
StepGen3 *Step = 0;
HardwareTimer *baseTimer;  // The base period timer
uint32_t sync0CycleTime;   // nanosecs, often 1000000 ( 1 ms )
volatile double posCmd1, posCmd2, posCmd3, posCmd4;
volatile float posScale1, posScale2, posScale3, posScale4;
volatile float maxAcc1, maxAcc2, maxAcc3, maxAcc4;
volatile uint8_t enable1, enable2, enable3, enable4;
volatile uint32_t basePeriod, newBasePeriod;
volatile uint16_t basePeriodCnt;
volatile uint16_t deltaMakePulsesCnt;
volatile uint64_t makePulsesCnt = 0;
void updateStepperGenerators(void);
void basePeriodCB(void);

///////// Spindle Encoder
#include "MyEncoder.h"
volatile uint16_t encCnt = 0;
void indexPulseEncoderCB1(void);
MyEncoder Encoder1(TIM2, PA3, indexPulseEncoderCB1);
void indexPulseEncoderCB1(void) {
  encCnt++;
  Encoder1.indexPulse();
}

///////// Frequency counter for Torch height
#include "HardwareTimer.h"
// NOTE This mod in the beginning (line 33) of HardwareTimer.cpp for 32-bit
// precision
////// //#define MAX_RELOAD ((1 << 16) - 1) // Currently even 32b timers are
///used as 16b to have generic behavior
////// #define MAX_RELOAD 0xFFFFFFFF
////// HardwareTimer.cpp is part of the Stm32duino code <add where to find that>

uint32_t channel;
volatile uint32_t FrequencyMeasured, LastCapture = 0, CurrentCapture;
uint32_t input_freq = 0;
volatile uint32_t rolloverCompareCount = 0;
HardwareTimer *FrequencyTimer;
void InputCapture_IT_callback(void);
void Rollover_IT_callback(void);

////// EtherCAT
const byte SYNC0 = PC3;
const byte SYNC1 = PC1;
const byte SINT = PC0;
volatile uint16_t ALEventIRQ;  // ALEvent that caused the interrupt
volatile byte serveIRQ =
    0;  // Flag indicating we got a SYNCx pulse and should act on that
volatile uint32_t globalIRQ = 0;               // Testing
extern "C" uint32_t ESC_SYNC0cycletime(void);  // A SOES function we need
void globalInt(void);                          // ISR for INT line

////// EtherCAT routines called regularly, to read data, do stuff and write data
void cb_set_outputs(void)  // Get Master outputs, slave inputs, first operation
{
  for (int i = 0; i < 4; i++)
    digitalWrite(OUTPUTS[i], bitcheck(Obj.Output4, i) ? HIGH : LOW);
  analogWrite(DAC1_pin, Obj.Voltage);
  Encoder1.setLatch(Obj.EncoderOut.IndexLatchEnable);
  Encoder1.setScale(Obj.EncoderOut.Scale);

  posScale1 = Obj.StepsPerMM1;  // Scale perhaps changed
  posScale2 = Obj.StepsPerMM2;
  posScale3 = Obj.StepsPerMM3;
  posScale4 = Obj.StepsPerMM4;
  posCmd1 = Obj.CommandedPosition1;  // The position update, etc
  posCmd2 = Obj.CommandedPosition2;  // Is recognised by the base Time loop
  posCmd3 = Obj.CommandedPosition3;
  posCmd4 = Obj.CommandedPosition4;
  maxAcc1 = Obj.MaxAcceleration1;
  maxAcc2 = Obj.MaxAcceleration2;
  maxAcc3 = Obj.MaxAcceleration3;
  maxAcc4 = Obj.MaxAcceleration4;
  enable1 = Obj.Enable1;
  enable2 = Obj.Enable2;
  enable3 = Obj.Enable3;
  enable4 = Obj.Enable4;
  if (Obj.BasePeriod != 0)  // Use default value from setup() if not set by SDO.
    newBasePeriod = Obj.BasePeriod;
}

void cb_get_inputs(void)  // Set Master inputs, slave outputs, last operation
{
  float scale = 1;
  if (Obj.EncoderOut.Scale != 0.0) scale = Obj.EncoderOut.Scale;

  for (int i = 0; i < 8; i++)
    if (digitalRead(INPUTS[i]) == HIGH)
      bitSet(Obj.Input8, i);
    else
      bitClear(Obj.Input8, i);

  Obj.EncoderIn.IndexStatus = Encoder1.indexHappened();
  Obj.EncoderIn.Position = Encoder1.currentPos();
  Obj.EncoderIn.IndexByte = Encoder1.getIndexState();
  Obj.EncoderIn.Velocity =
      Obj.EncoderOut.Scale * Encoder1.frequency(longTime.extendTime(micros()));

  Obj.ActualPosition1 = Step->stepgen_array[0].pos_fb;
  Obj.ActualPosition2 = Step->stepgen_array[1].pos_fb;
  Obj.ActualPosition3 = Step->stepgen_array[2].pos_fb;
  Obj.ActualPosition4 = Step->stepgen_array[3].pos_fb;
}

void handleStepper(
    void)  // Called every cycle, updates stepper generator with new positions,
           // restarts stepper generator and reads out current posution
{
  static int warned = 0;
  if (!warned &&
      sync0CycleTime ==
          0)  // This is kludge to be used during testing to activate stepper
              // during free run Stepper generators normally run only during
              // synchronized conditions. But to do testing.
  {
    sync0CycleTime = 1000000;  // 1e6 ns = 1e3 us = 1ms
    Serial1.println("Warn sync0Cycletime");
    warned = 1;
  }
  updateStepperGenerators();
}

void ESC_interrupt_enable(uint32_t mask);
void ESC_interrupt_disable(uint32_t mask);
uint16_t dc_checker(void);
void sync0Handler(void);

static esc_cfg_t config = {
    .user_arg = NULL,
    .use_interrupt = 0,
    .watchdog_cnt = 150,
    .set_defaults_hook = NULL,
    .pre_state_change_hook = NULL,
    .post_state_change_hook = NULL,
    .application_hook = handleStepper,
    .safeoutput_override = NULL,
    .pre_object_download_hook = NULL,
    .post_object_download_hook = NULL,
    .rxpdo_override = NULL,
    .txpdo_override = NULL,
    .esc_hw_interrupt_enable = ESC_interrupt_enable,
    .esc_hw_interrupt_disable = ESC_interrupt_disable,
    .esc_hw_eep_handler = NULL,
    .esc_check_dc_handler = dc_checker,
};

void setup(void) {
  Serial1.begin(115200);
  delay(1000);  // To make terminal window ready

  for (int i = 0; i < 4; i++) {
    pinMode(OUTPUTS[i], OUTPUT);
    digitalWrite(OUTPUTS[i], LOW);
  }
  for (int i = 0; i < 8; i++) pinMode(INPUTS[i], INPUT);
  pinMode(DAC1_pin, OUTPUT);
  analogWrite(DAC1_pin, 0);

  Step = new StepGen3;    // More settings in StepGen3.cpp and Stepgen3.h
  pinMode(PA11, OUTPUT);  // Step 1
  pinMode(PA12, OUTPUT);  // Dir 1
  pinMode(PC9, OUTPUT);   // Step 2
  pinMode(PC8, OUTPUT);   // Dir 2
  pinMode(PD12, OUTPUT);  // Step 3
  pinMode(PD11, OUTPUT);  // Dir 3
  pinMode(PE5, OUTPUT);   // Step 4
  pinMode(PE4, OUTPUT);   // Dir 4

  basePeriod = newBasePeriod = BASE_PERIOD;  // Random-ish number, but it should
                                             // work. Change through sdos

  baseTimer = new HardwareTimer(TIM11);  // The base period timer
  baseTimer->setOverflow(
      BASE_PERIOD / 1000,
      MICROSEC_FORMAT);  // Or the line above, This one is uncalibrated
  baseTimer->attachInterrupt(basePeriodCB);

  encoder_config();  // Needed by encoder, possibly breaks some timers.

  ecat_slv_init(&config);
  attachInterrupt(
      digitalPinToInterrupt(PC0), globalInt,
      RISING);  // For testing, should go into Enable_interrupt later on
}

void loop(void) {
  uint64_t dTime;
  if (serveIRQ) {
    DIG_process(DIG_PROCESS_WD_FLAG | DIG_PROCESS_OUTPUTS_FLAG |
                DIG_PROCESS_APP_HOOK_FLAG | DIG_PROCESS_INPUTS_FLAG);
    serveIRQ = 0;
    ESCvar.PrevTime = ESCvar.Time;
    ecat_slv_poll();
  }
  dTime = longTime.extendTime(micros()) - irqTime;
  if (dTime >
      5000)  // Don't run ecat_slv_poll when expecting to serve interrupt
    ecat_slv();
}

void sync0Handler(void) {
  ALEventIRQ = ESC_ALeventread();
  // if (ALEventIRQ & ESCREG_ALEVENT_SM2)
  {
    irqTime = longTime.extendTime(micros());
    serveIRQ = 1;
  }
}

// Enable SM2 interrupts
void ESC_interrupt_enable(uint32_t mask) {
  // Enable interrupt for SYNC0 or SM2 or SM3
  uint32_t user_int_mask =
      ESCREG_ALEVENT_DC_SYNC0 | ESCREG_ALEVENT_SM2 | ESCREG_ALEVENT_SM3;
  if (mask & user_int_mask) {
    ESC_ALeventmaskwrite(ESC_ALeventmaskread() | (mask & user_int_mask));
    ESC_ALeventmaskwrite(ESC_ALeventmaskread() &
                         ~(ESCREG_ALEVENT_DC_SYNC0 | ESCREG_ALEVENT_SM3));
    attachInterrupt(digitalPinToInterrupt(SYNC0), sync0Handler, RISING);

    // Set LAN9252 interrupt pin driver as push-pull active high
    uint32_t bits = 0x00000111;
    ESC_write(0x54, &bits, 4);

    // Enable LAN9252 interrupt
    bits = 0x00000001;
    ESC_write(0x5c, &bits, 4);
  }
}

// Disable SM2 interrupts
void ESC_interrupt_disable(uint32_t mask) {
  // Enable interrupt for SYNC0 or SM2 or SM3
  uint32_t user_int_mask =
      ESCREG_ALEVENT_DC_SYNC0 | ESCREG_ALEVENT_SM2 | ESCREG_ALEVENT_SM3;

  if (mask & user_int_mask) {
    // Disable interrupt from SYNC0 etc
    ESC_ALeventmaskwrite(ESC_ALeventmaskread() & ~(mask & user_int_mask));
    detachInterrupt(digitalPinToInterrupt(SYNC0));
    // Disable LAN9252 interrupt
    uint32_t bits = 0x00000000;
    ESC_write(0x5c, &bits, 4);
  }
}

// Setup of DC
uint16_t dc_checker(void) {
  // Indicate we run DC
  ESCvar.dcsync = 1;
  sync0CycleTime = ESC_SYNC0cycletime();  // nanosecs
  return 0;
}

// Test/debug routine for the INT line
void globalInt(void) { globalIRQ++; }

////// Frequency counter (torch height) callback routines
void InputCapture_IT_callback(void) {
  CurrentCapture = FrequencyTimer->getCaptureCompare(channel);

  /* frequency computation */
  if (CurrentCapture > LastCapture) {
    FrequencyMeasured = input_freq / (CurrentCapture - LastCapture);
  } else if (CurrentCapture <= LastCapture) {
    /* 0xFFFFFFFF is max overflow value */
    FrequencyMeasured =
        input_freq / (0xFFFFFFFF + CurrentCapture - LastCapture);
  }
  LastCapture = CurrentCapture;
  rolloverCompareCount = 0;
}

/* In case of timer rollover, frequency is to low to be measured set value to 0
   To reduce minimum frequency, it is possible to increase prescaler. But this
   is at a cost of precision. */
void Rollover_IT_callback(void) {
  rolloverCompareCount++;

  if (rolloverCompareCount > 1) {
    FrequencyMeasured = 0;
  }
}

///// Stepper generator callback routines
void updateStepperGenerators(void) {
  baseTimer->pause();
  Step->updateStepGen(posCmd1, posCmd2, posCmd3, posCmd4, posScale1, posScale2,
                      posScale3, posScale4, maxAcc1, maxAcc2, maxAcc3, maxAcc4,
                      enable1, enable2, enable3, enable4,
                      sync0CycleTime);  // Update positions
  Step->makeAllPulses();                // Make first step right here
  if (newBasePeriod != basePeriod)      // Changed via sdos
  {
    basePeriod = newBasePeriod;
    baseTimer->setOverflow(basePeriod / 1000,
                           MICROSEC_FORMAT);  // update timer frequency
  }
  basePeriodCnt = sync0CycleTime / basePeriod;  //
  baseTimer->refresh();                         //
  baseTimer->resume();
  // Make the other steps in baseTimer's ISR
}

void basePeriodCB(void) {
  if (--basePeriodCnt > 0)  // Stop
    Step->makeAllPulses();  // Make steps and pulses here
  else
    baseTimer->pause();
}

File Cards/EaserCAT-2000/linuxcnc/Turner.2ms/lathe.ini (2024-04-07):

# EMC controller parameters for a simulated machine.
# General note: Comments can either be preceded with a # or ; - either is
# acceptable, although # is in keeping with most linux config files.

# General section -------------------------------------------------------------
[EMC]
VERSION = 1.1
MACHINE =               gmoccapy_lathe
#DEBUG =               0x7FFFFFFF
DEBUG = 0

# for details see nc_files/subroutines/maco_instructions.txt
[DISPLAY]
DISPLAY = gmoccapy
LATHE = 1
BACK_TOOL_LATHE = 0

# Cycle time, in milliseconds, that display will sleep between polls
CYCLE_TIME =            100

# Highest value that will be allowed for feed override, 1.0 = 100%
MAX_FEED_OVERRIDE =     1.5
MAX_SPINDLE_OVERRIDE =  1.2
MIN_SPINDLE_OVERRIDE = .5

# Prefix to be used
PROGRAM_PREFIX = /home/debian/linuxcnc/nc_files

# Introductory graphic
INTRO_GRAPHIC = linuxcnc.gif
INTRO_TIME = 5

# list of selectable jog increments
INCREMENTS = 1.000 mm, 0.100 mm, 0.010 mm, 0.001 mm

[FILTER]
PROGRAM_EXTENSION = .png,.gif,.jpg Grayscale Depth Image
PROGRAM_EXTENSION = .py Python Script
png = image-to-gcode
gif = image-to-gcode
jpg = image-to-gcode
py = python

# Task controller section -----------------------------------------------------
[RS274NGC]
RS274NGC_STARTUP_CODE = G18 G21 G40 G49 G54 G80 G90 G94 G8 M9 M5 G64 P0.005
PARAMETER_FILE = sim.var
SUBROUTINE_PATH = macros

# Motion control section ------------------------------------------------------
[EMCMOT]
EMCMOT =              motmod
COMM_TIMEOUT =          1.0
BASE_PERIOD  =          100000
SERVO_PERIOD =          1000000

# Hardware Abstraction Layer section --------------------------------------------------
[TASK]
TASK =                  milltask
CYCLE_TIME =            0.001

# Part program interpreter section --------------------------------------------
[HAL]
HALFILE = core_sim_lathe.hal
HALFILE = spindle_sim.hal
HALFILE = simulated_home_lathe.hal

# Single file that is executed after the GUI has started.
POSTGUI_HALFILE = gmoccapy_postgui.hal

HALUI = halui

# Trajectory planner section --------------------------------------------------
[HALUI]
#No Content

[TRAJ]
COORDINATES =      X Z
LINEAR_UNITS =     mm
ANGULAR_UNITS =    degree
DEFAULT_LINEAR_VELOCITY = 50
MAX_LINEAR_VELOCITY = 234
POSITION_FILE =    position.txt
#NO_FORCE_HOMING = 1

# First axis
[EMCIO]
EMCIO = 		io
CYCLE_TIME =    0.100

# tool table file
TOOL_TABLE = lathe.tbl

[KINS]
KINEMATICS = trivkins coordinates=XZ
JOINTS = 2

[AXIS_X]
MIN_LIMIT = -50.0
MAX_LIMIT = 200.0
MAX_VELOCITY = 166
MAX_ACCELERATION = 1500.0

[JOINT_0]
TYPE =                          LINEAR
MAX_VELOCITY =                  166
MAX_ACCELERATION =              1500.0
BACKLASH = 0.000
INPUT_SCALE =                   4000
OUTPUT_SCALE = 1.000
MIN_LIMIT =                     -50.0
MAX_LIMIT =                     200.0
FERROR = 0.050
MIN_FERROR = 0.010
HOME_OFFSET =                    0.0
HOME =                           100
HOME_SEARCH_VEL =                200.0
HOME_LATCH_VEL =                 20.0
HOME_USE_INDEX =                 NO
HOME_IGNORE_LIMITS =             NO
HOME_SEQUENCE = 1
HOME_IS_SHARED = 1

# Third axis
[AXIS_Z]
MIN_LIMIT = -75.0
MAX_LIMIT = 1000.0
MAX_VELOCITY = 166
MAX_ACCELERATION = 1500.0

[JOINT_1]
TYPE =                          LINEAR
MAX_VELOCITY =                  166
MAX_ACCELERATION =              1500.0
BACKLASH = 0.000
INPUT_SCALE =                   4000
OUTPUT_SCALE = 1.000
MIN_LIMIT =                     -75.0
MAX_LIMIT =                     1000.0
FERROR = 0.050
MIN_FERROR = 0.010
HOME_OFFSET =                    1.0
HOME =                           250
HOME_SEARCH_VEL =                200.0
HOME_LATCH_VEL =                 20.0
HOME_USE_INDEX =                 NO
HOME_IGNORE_LIMITS =             NO
HOME_SEQUENCE = 0
HOME_IS_SHARED = 1

# section for main IO controller parameters -----------------------------------
[MACROS]
MACRO = i_am_lost
MACRO = halo_world
MACRO = jog_around
MACRO = increment xinc yinc
MACRO = go_to_position X-pos Y-pos Z-pos

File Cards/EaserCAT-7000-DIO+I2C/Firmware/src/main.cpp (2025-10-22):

#include <Arduino.h>
#include <stdio.h>
extern "C" {
#include "ecat_slv.h"
#include "utypes.h"
};
_Objects Obj;

#include "extend32to64.h"
extend32to64 longTime;

HardwareSerial Serial1(PA10, PA9);

uint8_t inputPin[] = {PD15, PD14, PD13, PD12, PD11, PD10,
                      PD9,  PD8,  PB15, PB14, PB13, PB12};
uint8_t outputPin[] = {PE10, PE9, PE8, PE7};

const uint32_t I2C_BUS_SPEED = 400000;
uint32_t I2C_restarts_1 = 0, I2C_restarts_2 = 0;
const uint8_t MCP3221_TYPE = 1, ADS1014_TYPE = 2;
int8_t old_I2Cdevice_1 = -1;
int8_t old_I2Cdevice_2 = -1;

#include "Wire.h"
TwoWire Wire2(PB11, PB10);

#include "MyMCP3221.h"
MyMCP3221 *mcp3221_1 = 0;
MyMCP3221 *mcp3221_2 = 0;

#include "ADS1X15.h"
ADS1014 *ads1014_1 = 0;
ADS1014 *ads1014_2 = 0;

void ads1014_reset(ADS1014 *ads) {
  ads->reset();
  ads->begin();
  ads->setGain(1);                 // 1=4.096V
  ads->setMode(0);                 // 0 continuous
  ads->setDataRate(6);             // Max for ads101x
  ads->readADC_Differential_0_1(); // This is the value we are interested in
}

#include <queue>
class OhmicSensing {
public:
  void handle(uint8_t voltageState, float inVoltage, float limitVoltage,
              float voltageDropLimit, uint32_t setupTime, uint16_t pulseLength,
              uint8_t enabled, uint8_t &sensed);

  // private:
  enum OhmicStates { OHMIC_IDLE, OHMIC_SETUP, OHMIC_PROBE, OHMIC_PULSE };
  OhmicStates ohmicState = OHMIC_IDLE;
  uint64_t startTime;
  uint64_t contactTime;
  float_t oldVoltage = 0.0;
  std::queue<float> voltages;
  float_t refVoltage;
};
OhmicSensing Ohm1;
OhmicSensing Ohm2;

void handleVoltageReader(float scale_in, float offset, float &outVoltage,
                         int32_t &outRaw, float &oldVoltage, float &oldRaw,
                         uint8_t devType, int8_t &old_devType,
                         uint8_t &readStat, uint32_t &outStatus, ADS1014 *&ads,
                         MyMCP3221 *&mcp, uint8_t I2C_address,
                         uint32_t &I2C_restarts);
void lowpassFilter(float &oldLowPassGain,
                   uint32_t &oldLowpassFilterPoleFrequency,
                   float &oldLowPassFilteredVoltage,
                   uint32_t LowpassFilterPoleFrequency,
                   float LowPassFilterThresholdVoltage, float inVoltage,
                   float &outFilteredVoltage);

#define bitset(byte, nbit) ((byte) |= (1 << (nbit)))
#define bitclear(byte, nbit) ((byte) &= ~(1 << (nbit)))
#define bitflip(byte, nbit) ((byte) ^= (1 << (nbit)))
#define bitcheck(byte, nbit) ((byte) & (1 << (nbit)))

extern "C" uint32_t ESC_SYNC0cycletime(void);

void cb_set_outputs(void) // Get Master outputs, slave inputs, first operation
{
  // Update digital output pins
  for (int i = 0; i < sizeof(outputPin); i++)
    digitalWrite(outputPin[i], bitcheck(Obj.Output4, i) ? HIGH : LOW);
}

float oldLowPassGain_1 = 0, oldLowPassGain_2 = 0;
float oldLowPassFilteredVoltage_1 = 0, oldLowPassFilteredVoltage_2 = 0;
uint32_t oldLowpassFilterPoleFrequency_1 = 0,
         oldLowpassFilterPoleFrequency_2 = 0;

void cb_get_inputs(void) // Set Master inputs, slave outputs, last operation
{
  static float validData0_1 = 0.0, validVoltage0_1 = 0.0;
  static float validData0_2 = 0.0, validVoltage0_2 = 0.0;
  uint8_t stat_1, stat_2;

  for (int i = 0; i < sizeof(inputPin); i++)
    Obj.Input12 = digitalRead(inputPin[i]) == HIGH ? bitset(Obj.Input12, i)
                                                   : bitclear(Obj.Input12, i);

  handleVoltageReader(Obj.In_Unit1.VoltageScale, Obj.In_Unit1.VoltageOffset,
                      Obj.Out_Unit1.CalculatedVoltage, Obj.Out_Unit1.RawData,
                      validVoltage0_1, validData0_1,
                      Obj.Settings_Unit1.I2C_devicetype, old_I2Cdevice_1,
                      stat_1, Obj.Out_Unit1.Status, ads1014_1, mcp3221_1,
                      Obj.Settings_Unit1.I2C_address, I2C_restarts_1);
  handleVoltageReader(Obj.In_Unit2.VoltageScale, Obj.In_Unit2.VoltageOffset,
                      Obj.Out_Unit2.CalculatedVoltage, Obj.Out_Unit2.RawData,
                      validVoltage0_2, validData0_2,
                      Obj.Settings_Unit2.I2C_devicetype, old_I2Cdevice_2,
                      stat_2, Obj.Out_Unit2.Status, ads1014_2, mcp3221_2,
                      Obj.Settings_Unit2.I2C_address, I2C_restarts_2);
  lowpassFilter(oldLowPassGain_1, oldLowpassFilterPoleFrequency_1,
                oldLowPassFilteredVoltage_1,
                Obj.Settings_Unit1.LowpassFilterPoleFrequency,
                Obj.In_Unit1.LowPassFilterThresholdVoltage,
                Obj.Out_Unit1.CalculatedVoltage,
                Obj.Out_Unit1.LowpassFilteredVoltage);
  lowpassFilter(oldLowPassGain_2, oldLowpassFilterPoleFrequency_2,
                oldLowPassFilteredVoltage_2,
                Obj.Settings_Unit2.LowpassFilterPoleFrequency,
                Obj.In_Unit2.LowPassFilterThresholdVoltage,
                Obj.Out_Unit2.CalculatedVoltage,
                Obj.Out_Unit2.LowpassFilteredVoltage);

  Ohm1.handle(stat_1, Obj.Out_Unit1.CalculatedVoltage,
              Obj.In_Unit1.OhmicSensingVoltageLimit,
              Obj.In_Unit1.OhmicSensingVoltageDrop,
              Obj.Settings_Unit1.OhmicSensingSetupTime,
              Obj.Settings_Unit1.OhmicSensingPulseLength,
              Obj.In_Unit1.EnableOhmicSensing,
              Obj.Out_Unit1.OhmicSensingSensed);
  Ohm2.handle(stat_2, Obj.Out_Unit2.CalculatedVoltage,
              Obj.In_Unit2.OhmicSensingVoltageLimit,
              Obj.In_Unit2.OhmicSensingVoltageDrop,
              Obj.Settings_Unit2.OhmicSensingSetupTime,
              Obj.Settings_Unit2.OhmicSensingPulseLength,
              Obj.In_Unit2.EnableOhmicSensing,
              Obj.Out_Unit2.OhmicSensingSensed);
  Obj.Out_Unit1.RawData = (int)Ohm2.ohmicState;
}

uint16_t dc_checker(void);

static esc_cfg_t config = {
    .user_arg = NULL,
    .use_interrupt = 1,
    .watchdog_cnt = 150,
    .set_defaults_hook = NULL,
    .pre_state_change_hook = NULL,
    .post_state_change_hook = NULL,
    .application_hook = NULL,
    .safeoutput_override = NULL,
    .pre_object_download_hook = NULL,
    .post_object_download_hook = NULL,
    .rxpdo_override = NULL,
    .txpdo_override = NULL,
    .esc_hw_interrupt_enable = NULL,
    .esc_hw_interrupt_disable = NULL,
    .esc_hw_eep_handler = NULL,
    .esc_check_dc_handler = dc_checker,
};

void setup(void) {
  Serial1.begin(115200);

  for (int i = 0; i < sizeof(inputPin); i++)
    pinMode(inputPin[i], INPUT_PULLDOWN);
  for (int i = 0; i < sizeof(outputPin); i++) {
    pinMode(outputPin[i], OUTPUT);
    digitalWrite(outputPin[i], LOW);
  }
  // Debug leds
  pinMode(PB4, OUTPUT);
  pinMode(PB5, OUTPUT);
  pinMode(PB6, OUTPUT);
  pinMode(PB7, OUTPUT);
  digitalWrite(PB4, LOW);
  digitalWrite(PB5, LOW);
  digitalWrite(PB6, LOW);
  digitalWrite(PB7, LOW);

  Wire2.begin();
  Wire2.setClock(I2C_BUS_SPEED);

#ifdef ECAT
  ecat_slv_init(&config);
#endif
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

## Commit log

2023-12-21 Fixed 4-layer files
    [Ethercat-stm32.kicad_pcb]
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2023-12-25 After making board no 2. work
    [LAN9252.kicad_sch]
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2023-12-26 Added linuxcnc files
    [Turner.hal]
2023-12-28 New pcb
    [AX48100.kicad_sch, AX58100_phy_etc.kicad_sch, Ax58100-stm32-ethercat.csv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]
2023-12-28 Updates to encoder
    [Turner.hal]
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2023-12-31 Geographic annotation on pcb 2
    [AX48100.kicad_sch, AX58100_phy_etc.kicad_sch, Ax58100-stm32-ethercat.kicad_pcb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]
2023-12-31 Reshuffle file structure
    [AX48100.kicad_sch, AX58100_phy_etc.kicad_sch, Ax58100-stm32-ethercat.csv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]
2023-12-31 Tested, works in linuxcnc, doesn't work in free run mode
    [main.cpp]
2024-01-01 wip, stepper doesn't run
    [main.cpp]
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2024-01-02 Bugs found. set duty cycle after overflow()
    [main.cpp]
2024-01-04 Now it is occasionally updating correct 1 ms. wip.
    [main.cpp]
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2024-01-06 Added linuxcnc test config before video release
    [Turner.hal, Turner.ini, axis_manualtoolchange.hal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]
2024-01-09 It seems to work now, with reload in the timer_CB. Avoid micros()
    [main.cpp]
2024-01-10 New gerber files for ax58100 for pcb quotations
    [Ax58100-stm32-ethercat-B_Cu.gbr, Ax58100-stm32-ethercat-B_Mask.gbr, Ax58100-stm32-ethercat-B_Paste.gbr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]
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2024-01-15 Still problem with overlapping cycles in stepgen. TIM8 works for stepgen now.
    [StepGen.cpp, main.cpp]
2024-01-15 Bug, digitalWrite of stepPin should be dirPin in timerCB. Reshuffling
    [StepGen.cpp]
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2024-01-18 TIM8 replaced with TIM3. TIM3,chan4 works on PC9. TIM8,chan4 should work but doesn't. How should one know?
    [StepGen.cpp, main.cpp]
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2024-01-20 Added optional pull-down to step generators
    [Ax58100-stm32-ethercat.kicad_pcb, STM32F4.kicad_sch, peripherals.kicad_sch]
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2024-01-21 wip inputs with photodiodes etc
    [peripherals.kicad_sch]
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2024-01-23 How many times to fix it?
    [main.cpp]
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2024-01-23 Cleaning old gerber files.
    [Ax58100-stm32-ethercat-B_Cu.gbr, Ax58100-stm32-ethercat-B_Mask.gbr, Ax58100-stm32-ethercat-B_Paste.gbr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]
2024-01-23 Wip optocoupler input and outputs
    [peripherals.kicad_sch]
2024-01-24 Steppers, encoders, IO, etc remapped
    [AX48100.kicad_sch, AX58100_phy_etc.kicad_sch, Ax58100-stm32-ethercat.csv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]
2024-01-24 Assigned footprints
    [STM32F4.kicad_sch, Steppers.kicad_sch, peripherals.kicad_sch]
2024-01-24 First component placement
    [Ax58100-stm32-ethercat.kicad_pcb, STM32F4.kicad_sch, Steppers.kicad_sch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]
2024-01-24 Two-layer now
    [Ax58100-stm32-ethercat.kicad_pcb]
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2024-01-25 Might be in final shape.
    [AX48100.kicad_sch, AX58100_phy_etc.kicad_sch, Ax58100-stm32-ethercat.kicad_pcb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]
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2024-01-26 Added 4k7 pullup onm scs_func. Think not needed since it is to a pin on stm32, but in case
    [AX48100.kicad_sch, Ax58100-stm32-ethercat.kicad_pcb]
2024-01-26 all leds are now 0603
    [AX58100_phy_etc.kicad_sch, Ax58100-stm32-ethercat.kicad_pcb, STM32F4.kicad_sch]
2024-01-26 morfe copper in +5V leads
    [Ax58100-stm32-ethercat.kicad_pcb]
2024-01-26 Getting ready for fab
    [AX48100.kicad_sch, AX58100_phy_etc.kicad_sch, Ax58100-stm32-ethercat.kicad_pcb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]
2024-01-26 Fab from this version
    [Ax58100-stm32-ethercat.kicad_pcb]
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2024-02-09 Clear ALevents for DC_sync0 and SM3 might have solved the uneven pulse train. Looking better now.
    [StepGen2.cpp, StepGen2.h, main.cpp]
2024-02-11 a cycle's pwm train maight have been too long and run into the start of next cycle's pwm train. That's gone now and it seems to work. A more brilliant solution is needed for this.
    [StepGen2.cpp, StepGen2.h, main.cpp]
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2024-03-13 Fixed bug in extend32to64:extendTime()
    [StepGen2.cpp, StepGen2.h, main.cpp]
2024-03-17 Yes it works now. Made another implementation of the pulse IRQ and all that. We'll see if I keep this or go back to the older. It is IMPORTANT, REQUIRED to use a 4.9 linux kernel for it to work. Ther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
    [StepGen2.cpp, StepGen2.h, main.cpp]
2024-03-20 It works. I hate RealTek. Even with the r8618_dkms driver it doesn't work. I bought a Intel network card, set irq coalesce rx-usecs and tx-usecs to 0. Now it works works WORKS. No lost packages, no d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
    [StepGen2.cpp, StepGen2.h, main.cpp]
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2024-03-23 Shortest BASE_PERIOD is 12000 as it is now. Plus some cleanup
    [StepGen3.h, main.cpp]
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2024-03-27 Didn't help using TICK_FORMAT in setOverflow()
    [main.cpp]
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2024-04-03 Added max irq time and jitter time measurement
    [main.cpp]
2024-04-04 jitter flawed, removed
2024-04-05 FIx 1c13 index manually, nLoops is back
    [StepGen3.h, main.cpp]
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2024-04-07 Working linuxcnc lathe config with 2 ms cycle time
    [Turner.hal, Turner.ini, core_sim_lathe.hal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]
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2024-04-10 Replaced runningaverage (uses malloc) with CircularBuffer
    [main.cpp]
2024-04-12 Tried to extrapolate when missing position data. Didn't work as expected but I'll keep it.
    [StepGen3.h, main.cpp]
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2024-04-14 Added study of OS version, NICs, computers to see what cycle times are reliable
    [Performance.ods]
2024-11-20 Ny structure. Start of the "main" branch
    [8In-8Out-LAN9252-only-B_Cu.gbr, 8In-8Out-LAN9252-only-B_Mask.gbr, 8In-8Out-LAN9252-only-B_Paste.gbr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]
2024-11-21 Moving all to Kicad8. Housekeeping symbols,libraries,3d-models
    [AX48100.kicad_sch, AX58100_phy_etc.kicad_sch, Ax58100-stm32-ethercat.kicad_pcb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]
2024-11-25 Updated 24V field voltage routing. Files sent for fab
    [8In-8Out-LAN9252-only.kicad_pcb, LAN9252.kicad_sch, LAN9252_diverse.kicad_sch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]
2024-11-25 Updated reset circuit to PB12
    [Ax58100-stm32-ethercat.kicad_pcb, STM32F4.kicad_sch]
2024-11-25 Removed Gerbers. Generate them as needed instead
    [8In-8Out-LAN9252-only-B_Cu.gbr, 8In-8Out-LAN9252-only-B_Mask.gbr, 8In-8Out-LAN9252-only-B_Paste.gbr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]
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2024-12-10 Updates to hw straps after startup of card.
    [8In-8Out-LAN9252-only.kicad_pcb, LAN9252.kicad_sch, LAN9252_diverse.kicad_sch]
2024-12-14 Submitting design for fabrication
    [J0011D01BNL_3D.STEP, LAN9252_DIO_SPI.kicad_sch, LAN9252_diverse.kicad_sch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]
2025-01-11 Modified, switch marker postions for C28 and R17
    [LAN9252_DIO_SPI.kicad_sch, LAN9252_diverse.kicad_sch, STM32F4.kicad_sch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]
2025-01-12 Fixed placement of Out1-Out4 diodes' marking
    [THCAD-reader+Digital-IO.kicad_pcb]
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2025-02-13 Branch mess fix
    [THTIC.kicad_pcb, THTIC.kicad_sch, THTIC2.kicad_pcb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]
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2025-02-14 Works in TwinCAT. Prepare for test in machine.
    [THTIC.kicad_sch]
2025-02-15 R19 C27 Bug. Fixed.
    [EaserCAT-7000.kicad_pcb]
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2025-02-16 Fixed R17 C28 label position bug
    [THCAD-reader+Digital-IO.kicad_pcb]
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2025-02-16 Ordered the real version
    [THTIC.kicad_pcb, THTIC.kicad_sch]
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2025-02-19 Name change of E7000
    [EaserCAT-7000.kicad_pcb, EaserCAT-7000.kicad_sch, I2C.kicad_sch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]
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2025-02-20 SCL instead of SDL
    [THTIC2.kicad_pcb]
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2025-02-21 Final version of THTIC2
    [THTIC.kicad_pcb, THTIC2.kicad_pcb, THTIC2.kicad_sch]
2025-02-25 Now measuring 0 - -200 Volts.
    [THTIC.kicad_pcb, THTIC.kicad_sch]
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2025-03-08 Shifted pin 0 and pin 1 for positive voltage value.
    [THTIC2.kicad_pcb, THTIC2.kicad_sch]
2025-03-09 Added missing Viso connection to IS1540
    [THTIC.kicad_pcb]
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2025-04-26 THTIC3 - copy of THTIC
    [THTIC3.kicad_pcb, THTIC3.kicad_sch]
2025-04-27 Renamed to THCLIP. Version 1.
    [THCLIP.kicad_pcb, THCLIP.kicad_sch, THTIC3.kicad_pcb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]
2025-04-28 Added selection criteria for relay in Schematics
    [THCLIP.kicad_sch]
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2025-06-07 updated process description more
    [THCLIP.kicad_sch]
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2025-08-17 Moved PDOs to SDOs, made an example config
    [axis.ini, e3000.hal]
2025-08-17 After testing, seems to work. Not tested: encoder,frequency,dac
    [e3000.hal]
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2025-10-07 Updated short-circuit resistor to 4k7 for more stable voltage.
    [THCLIP.kicad_pcb, THCLIP.kicad_sch]
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2025-10-19 Apply voltage on work piece, not torch cable Also read voltage on work piece
    [THCLIP.kicad_sch]
2025-10-21 Updated to read voltage from ground clamp instead of ground in the plasma, which obviously isn't the´real thing.
    [THCLIP.kicad_pcb, THCLIP.kicad_sch]
